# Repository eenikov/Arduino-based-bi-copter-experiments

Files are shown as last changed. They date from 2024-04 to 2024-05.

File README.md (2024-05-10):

# System Identification and Control Design Experiments with the Arduino-Based Bi-Copter Hardware 
## Eniko T Enkiov, University of Arizona
This project aims to demonstrate the use of MATLAB's system identification toolbox in developing dynamic models of an Arduino-Based aero-mechatronic system. The system is comprised of two propellers mounted on a pivoting arm, along with Arduino Nano 33 IoT and a battery pack. It is operated wirelessly via local WiFi network using MATLAB's Simulink Arduino support package. Except for the 3D printed arm and stand, all other components are commercially available, allowing easy replication of the experiment. Additionally, a Simscape model replicates the hardware-based experience for users who prefer virtual experimentation.
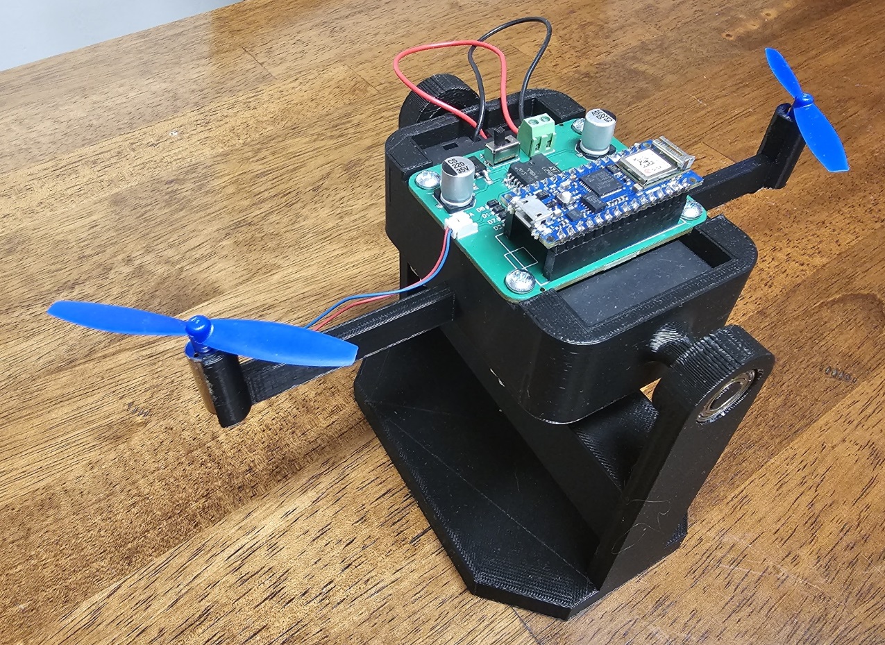
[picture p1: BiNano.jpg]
  

https://github.com/eenikov/BiCopter_SystemID_Project/assets/116908311/2a8902c1-a9a7-4af2-bafb-f2ca30b6aef8

## Learning Goals
- Obtain linear dynamic models from input-output data. Examples inlucde autoregressive models with exogenous input (ARX), state space model based on N4SID subspace method.
- Investigate the the effect of bandwidth and amplitude of the test input on the obtained model. 
- Evaluate different model orders using physical and numerical considerations (creiteria such as autocorrelelation and cross correlation of the resiudual)
- Learn how to design closed-loop controllers using PID and state space-based approaches. 

## Setup
- [Bi-copter 3D printing instructions](https://www.youtube.com/watch?v=3kPK0pJ30wg) (Download [SolidWorksFiles.zip](https://github.com/eenikov/BiCopter_SystemID_Project/blob/main/SolidWorksFiles.zip) and print  Stand, Arms, and 2x Bearing Caps using a 3D printer of your choice.)
-Download the controller circuit board files [PCB.zip](https://github.com/eenikov/BiCopter_SystemID_Project/blob/main/PCB.zip) and place an order with [https://jlcpcb.com/](https://jlcpcb.com/) to produce a PCB with the motor drivers. You will need to purchase the reaming parts from AMAZON.COM and assemble the pendulum per the instructions in the video below.
-  Download the bill of materials/parts [Bill_of_Materials.xlsx](https://github.com/eenikov/Arduino-based-bi-copter-experiments/blob/main/Bill_Of_Materials.xlsx) and purchase from AMAZON or other vendor of your choice.
- [Follow the Bi-Copter assembly instructions](https://www.youtube.com/watch?v=vzXoB-3JaGU)
- Download and install low-cost hardware support packages:
  * [Simulink Support Package for Arduino](https://www.mathworks.com/hardware-support/arduino.html#simulink)
  * [MATLAB Support Package for Arduino](https://www.mathworks.com/hardware-support/arduino.html#matlab)
 
## Experiments with the physical hardware (based on Livescript and three Simulink models operating the Bi-Copter
- Download [Bicopter_Hardware_Experiments](https://github.com/eenikov/Arduino-based-bi-copter-experiments/tree/main/Bicopter_Hardware_Experiments) repository and launch  [Run_Bicopter_Experiments.mlx](https://github.com/eenikov/Arduino-based-bi-copter-experiments/blob/main/Bicopter_Hardware_Experiments/Run_Bicopter_Experiments.mlx) live script. Follow instructions with the script. Run section by section.

## Experiments with a Simscape Model (alternative to the physical experiment)
- Download [Bicopter_Virtual_Experiments](https://github.com/eenikov/Arduino-based-bi-copter-experiments/tree/main/Bicopter_Virtual_Experiments) repository and launch [BiCopter_Simulation.mlx](https://github.com/eenikov/Arduino-based-bi-copter-experiments/blob/main/Bicopter_Virtual_Experiments/BiCopter_Simulation.mlx)  live script. Follow instructions with the Live Script. Run section by section.

## Additional Resources
- [System Identification Tech Talks](https://www.mathworks.com/videos/series/system-identification.html)
- [MATLAB Onramp](https://www.mathworks.com/learn/tutorials/matlab-onramp.html) – a free two-hour introductory tutorial that teaches the essentials of MATLAB.
- [Simulink Onramp](https://www.mathworks.com/learn/tutorials/simulink-onramp.html) – a free three-hour introductory tutorial that teaches the essentials of Simulink.
- [Control Design Onramp with Simulink](https://matlabacademy.mathworks.com/details/control-design-onramp-with-simulink/controls) - learn the basics of feedback control design in Simulink.

## Products
MATLAB, Simulink, System Identification Toolbox™, Control System Toolbox™, Simscape™, Simscape Multibody™

## Educator Resources
- [MATLAB and Simulink Courseware](https://www.mathworks.com/academia/courseware.html)
- [Teaching Controls with MATLAB and Simulink](https://www.mathworks.com/academia/courseware/teaching-controls-with-matlab-and-simulink.html)
- [Teaching Modeling and Controls using MATLAB Live Scripts](https://www.mathworks.com/videos/teaching-modeling-and-controls-with-the-matlab-live-editor-1623992486476.html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)

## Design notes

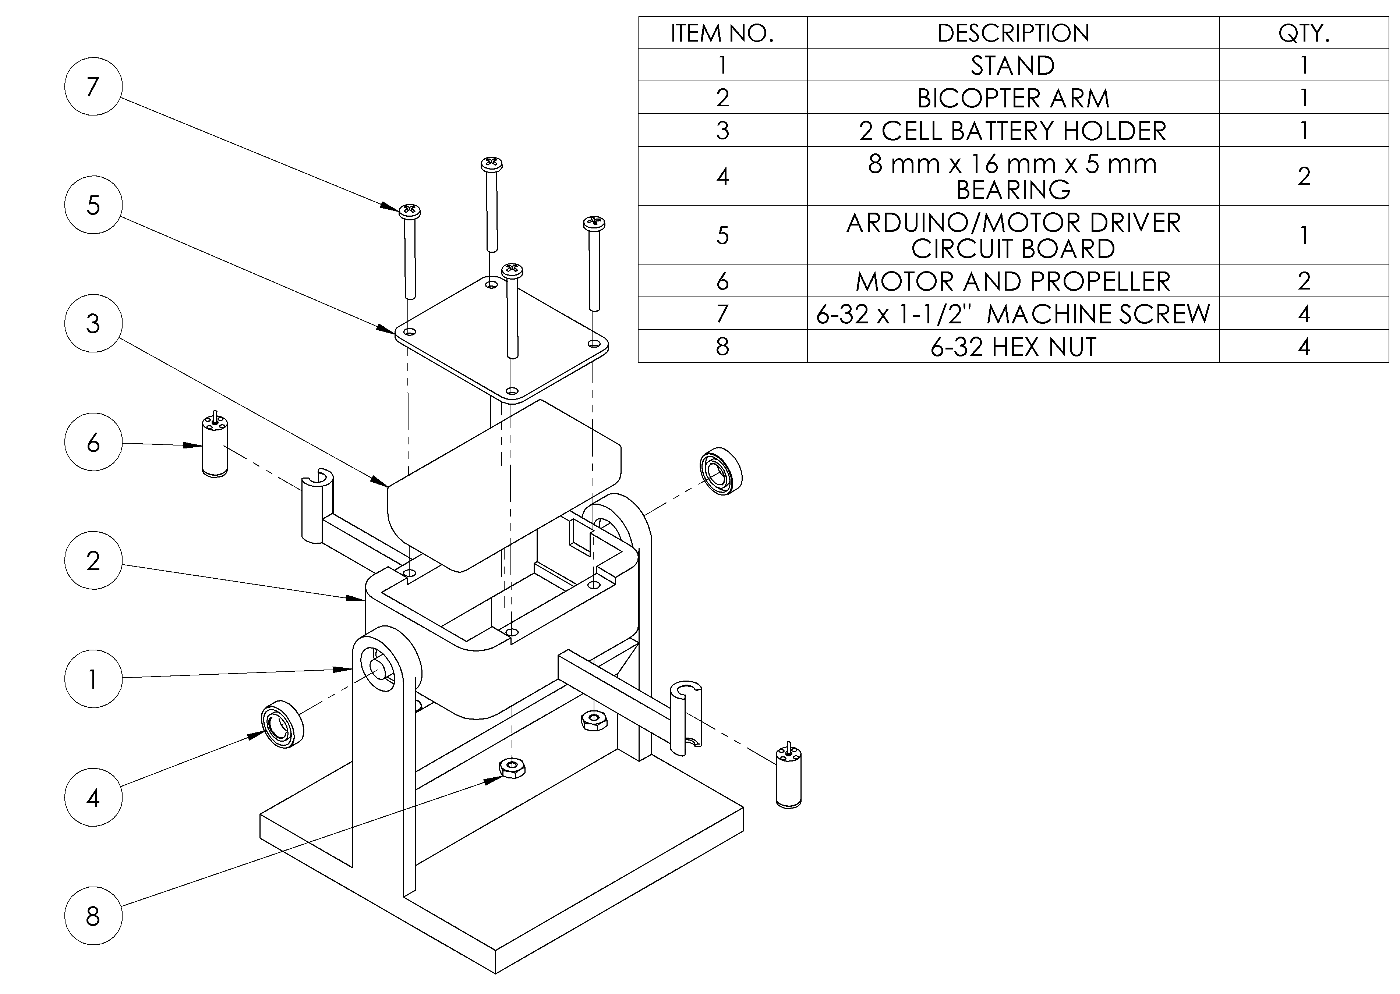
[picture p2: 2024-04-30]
SolidWorksFiles/Assem1.PNG

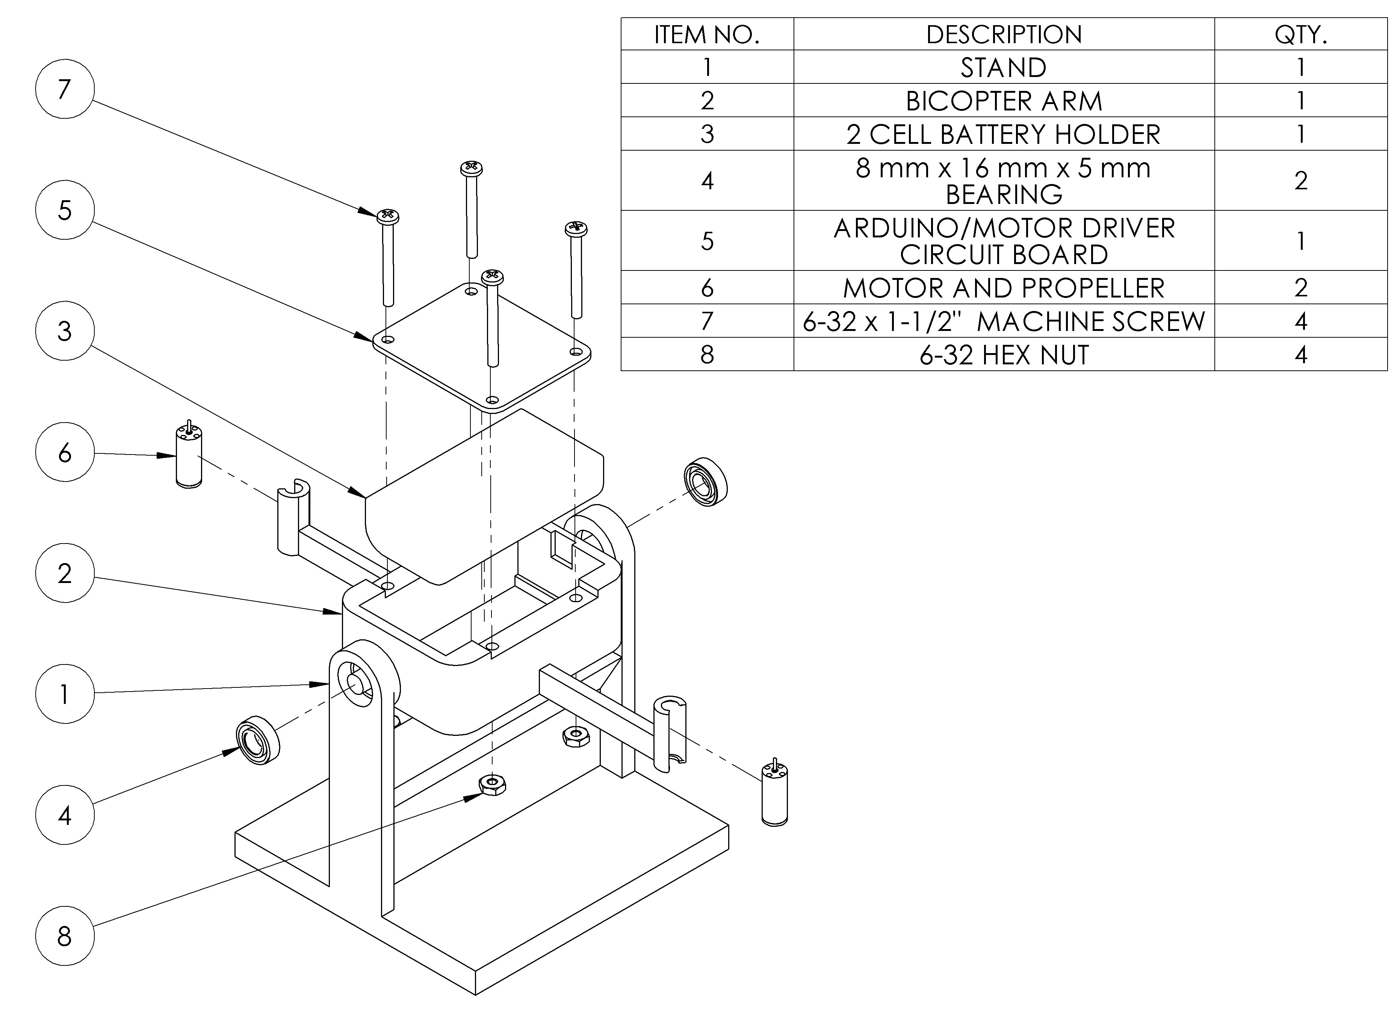
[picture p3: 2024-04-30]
SolidWorksFiles/Assem1.JPG

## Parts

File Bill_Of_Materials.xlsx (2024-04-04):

ITEM NO. | DESCRIPTION | QTY. | AMAZON LINK
1 | STAND | 1
2 | BICOPTER ARM | 1
4 | 8 mm x 16 mm x 5 mm BEARING | 2 | https://www.amazon.com/uxcell-Bearing-Shielded-2080088-Bearings/dp/B07FW2YKL8/
6 | MOTOR AND PROPELLER | 2 | https://www.amazon.com/Funny-Utopic-8-5x20mm-Connector-Quadcopter/dp/B07PLV3C2K https://www.amazon.com/dp/B019W2QDNO/
5 | 6-32 x 1-1/2" MACHINE SCREW (OR M4X35) | 4 | https://www.amazon.com/Prime-Line-9003284-Machine-Phillips-Stainless/dp/B074ZZ2K8Z/
6 | 6-32 HEX NUT (OR M4) | 4 | https://www.amazon.com/Prime-Line-9074040-Machine-Stainless-50-Pack/dp/B074ZMZZKS/
7 | ARDUINO/MOTOR DRIVER CIRCUIT BOARD | 1
8 | 2 CELL BATTERY HOLDER | 1 | https://www.amazon.com/Battery-Storage-Plastic-Batteries-YOUCHENG/dp/B08LZ3553W/ https://www.amazon.com/TOPUSSE-Rechargeable-Battery-2500mAh-Current/dp/B0C1NNXKW1/?th=1

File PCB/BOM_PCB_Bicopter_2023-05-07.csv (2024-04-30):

ID | Name | Designator | Footprint | Quantity | Manufacturer Part | Manufacturer | Supplier | Supplier Part | Price
1 | AS7805ADTR-G1 | U1 | TO-252-2_L6.6-W6.1-P4.57-LS9.9-BR-CW | 1 | AS7805ADTR-G1 | DIODES(美台) | LCSC | C294595 | 0.219
2 | POWER | SW1 | SW-TH_SS-12D02-VG4 | 1 | SS-12D02-VG4 | Rectangular Connectors - Contacts | LCSC | C136719 | 0.073
3 | 220uF | U4,U5 | CAP-SMD_BD8.0-L8.3-W8.3-FD | 2 | CS220UF35V167RV0148 | KNSCHA(科尼盛) | LCSC | C5250965 | 0.07
4 | L298P | U6 | POWERSO20_L15.9-W11.0-P1.27-LS14.2-BL-EP | 1 | L298P | ST(意法半导体) | LCSC | C85595 | 12.272
5 | Vin | U9 | CONN-TH_2P-P3.50_JL124D-35002G01 | 1 | JL124D-35002G01 | JILN | LCSC | C415432 | 0.142
6 | MOTOR A | CN1 | CONN-TH_530480210 | 1 | 530480210 | MOLEX | LCSC | C505099 | 0.155
7 | MOTOR B | CN2 | CONN-TH_530480210 | 1 | 530480210 | MOLEX | LCSC | C505099 | 0.155
8 | HDR-F-2.54_1x15 | H1,H2 | HDR-F-2.54_1X15 | 2 |  |  | LCSC | C124408 | 0.204
9 | 1N4007-C181127 | D1,D2,D3,D4,D5,D6,D7,D8 | SOD-123F_L2.8-W1.8-LS3.7-RD | 8 | 1N4007L | Hottech(合科泰) | LCSC | C181127 | 0.007

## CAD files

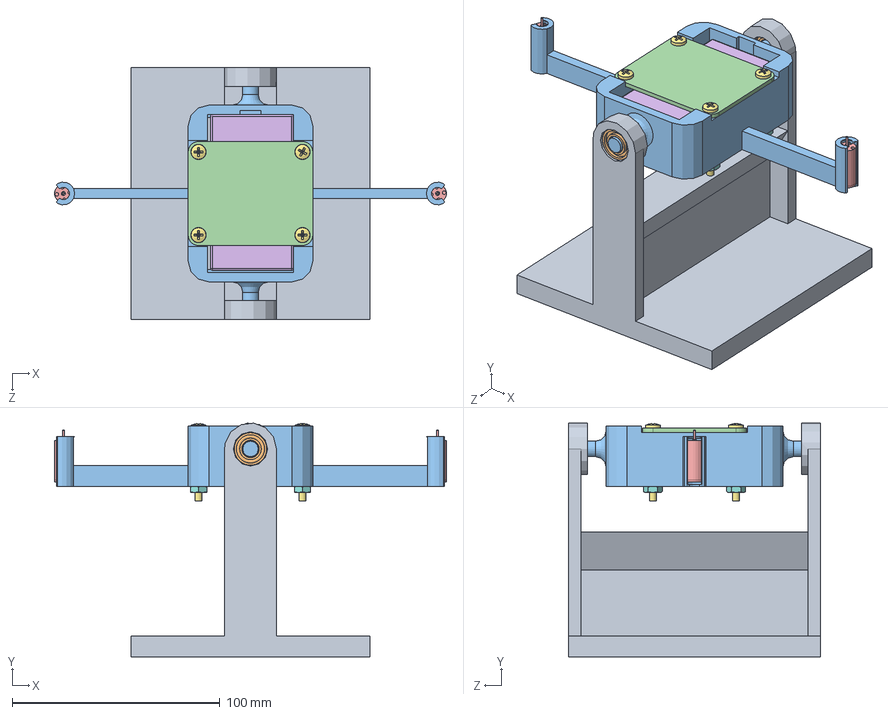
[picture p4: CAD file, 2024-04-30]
SolidWorksFiles/Assem1.SLDASM
188.5 x 112.4 x 121.0 mm
stand
radial ball bearing_68_am x 2
arms
board
8520 Coreless Brshed motor.step x 2
battery_holder
binding head screw_ai x 4
machine screw nut hex_ai x 4

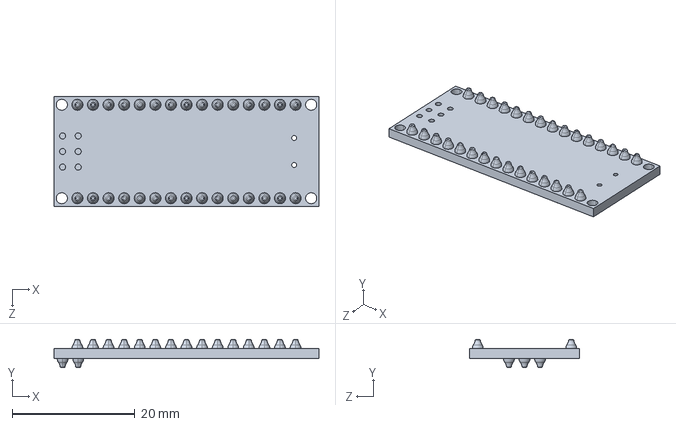
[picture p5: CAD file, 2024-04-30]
Bicopter_Virtual_Experiments/nano-board_Default_sldprt.STEP
43.2 x 4.60 x 18.0 mm

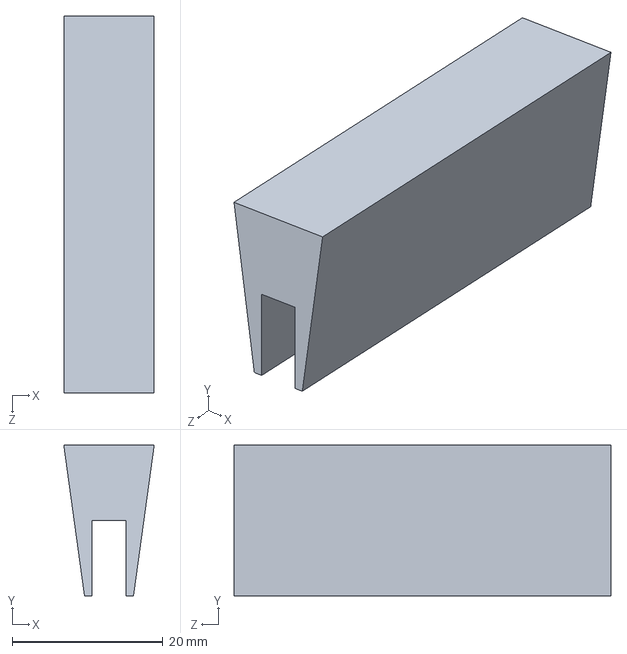
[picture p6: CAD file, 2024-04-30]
SolidWorksFiles/spacer.SLDPRT
12.0 x 20.0 x 50.0 mm

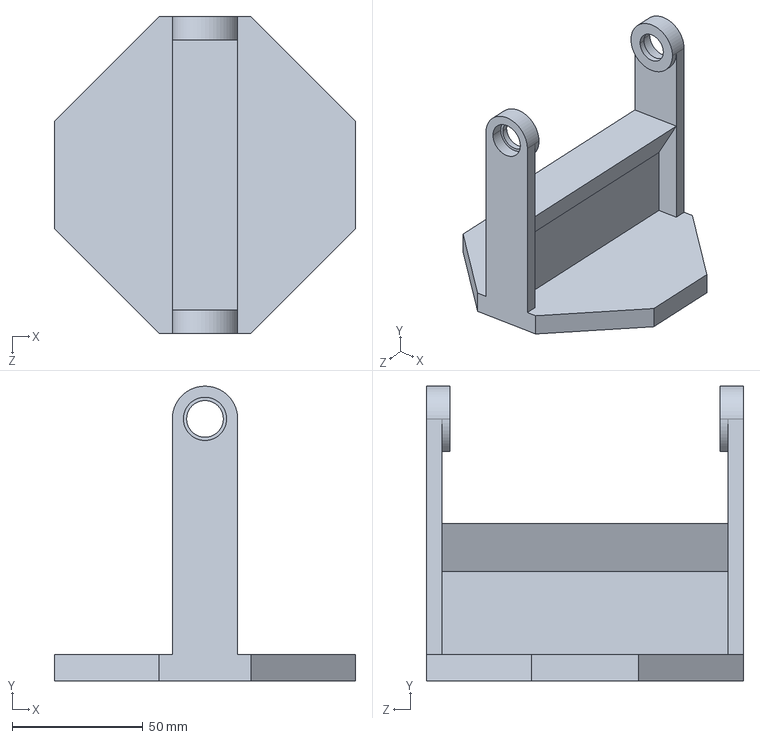
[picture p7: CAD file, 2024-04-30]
Bicopter_Virtual_Experiments/stand_Default_sldprt.STEP
115.0 x 112.5 x 121.0 mm

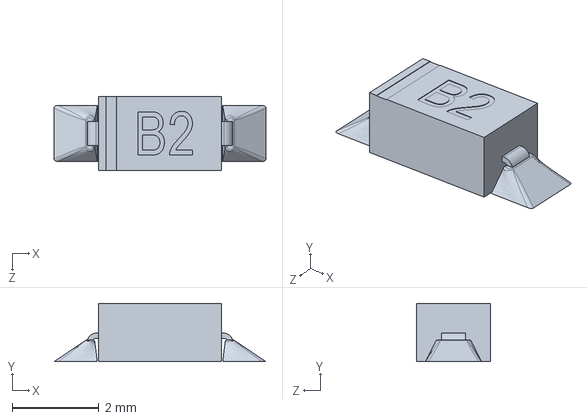
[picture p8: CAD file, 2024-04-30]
Bicopter_Virtual_Experiments/NANO DIODE_Default_sldprt.STEP
4.90 x 1.35 x 1.70 mm

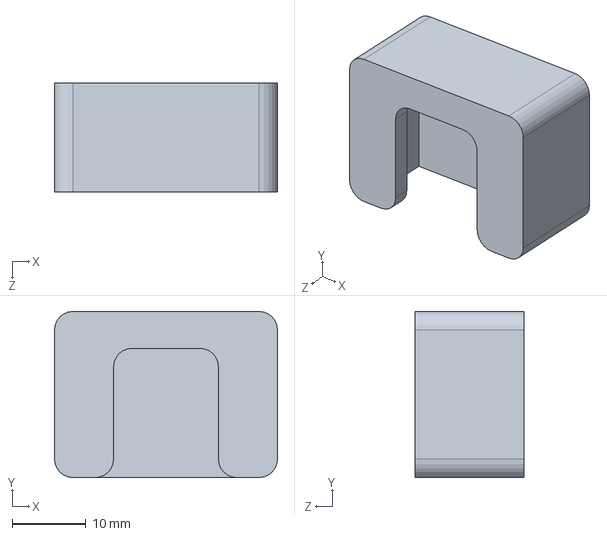
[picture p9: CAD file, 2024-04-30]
SolidWorksFiles/Ball Bearing Cap.SLDPRT
30.2 x 22.5 x 14.8 mm

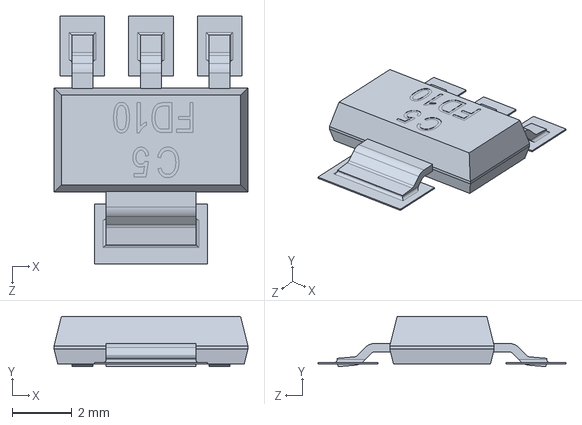
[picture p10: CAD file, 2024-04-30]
Bicopter_Virtual_Experiments/nano - reg_Default_sldprt.STEP
6.50 x 1.69 x 8.30 mm

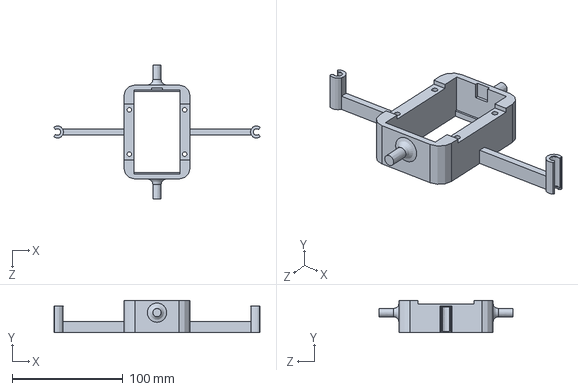
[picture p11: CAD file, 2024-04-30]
SolidWorksFiles/arms.SLDPRT
186.4 x 29.0 x 121.0 mm

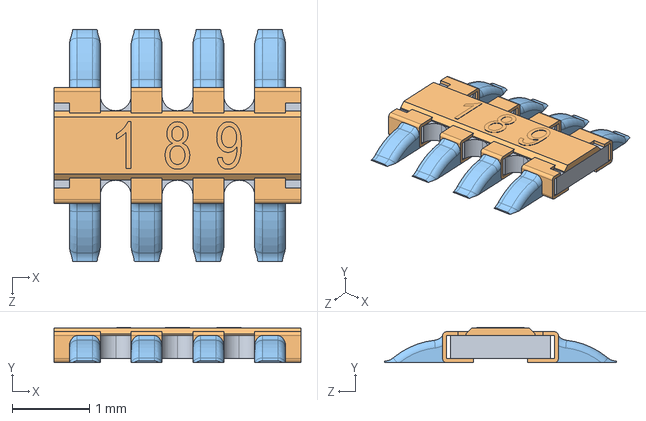
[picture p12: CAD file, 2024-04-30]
Bicopter_Virtual_Experiments/189 RESISTOR PACK_Default_sldprt.STEP
3.20 x 0.455 x 3.00 mm

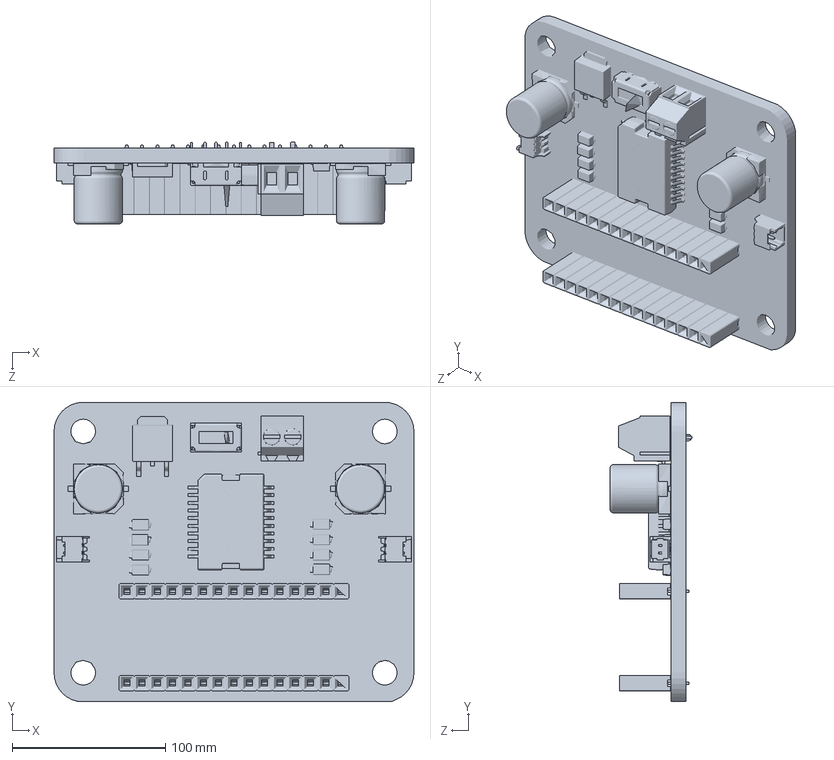
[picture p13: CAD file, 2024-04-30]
SolidWorksFiles/OBJ_PCB_Bicopter.SLDPRT
235.0 x 195.5 x 53.3 mm

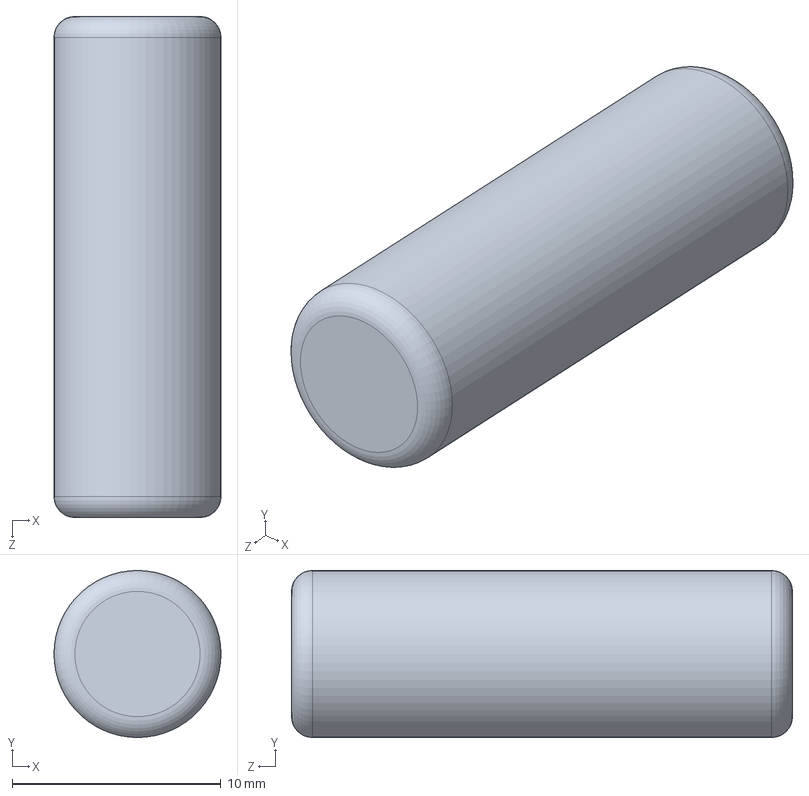
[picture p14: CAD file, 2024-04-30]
Bicopter_Virtual_Experiments/motor.SLDPRT
8.00 x 8.00 x 24.0 mm

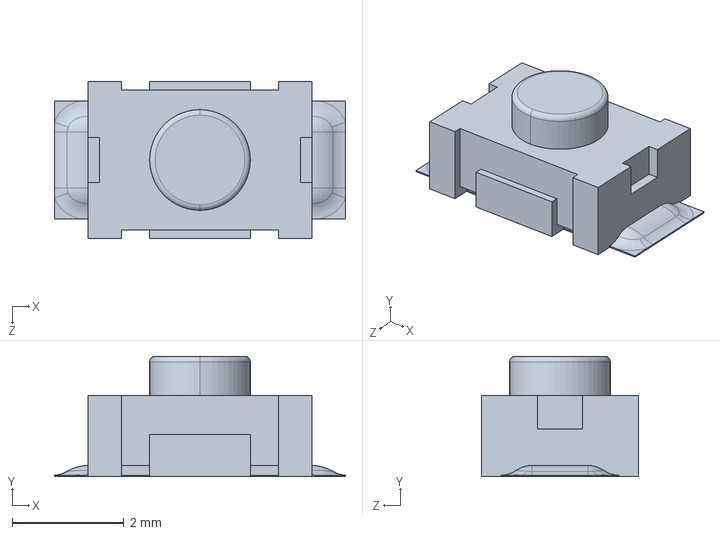
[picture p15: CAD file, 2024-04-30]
Bicopter_Virtual_Experiments/reset core_Default_sldprt.STEP
5.20 x 2.15 x 2.80 mm

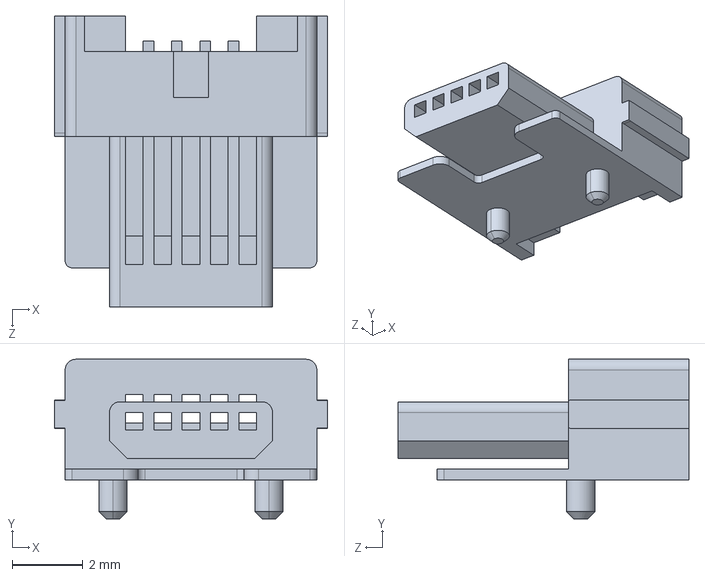
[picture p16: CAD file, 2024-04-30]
Bicopter_Virtual_Experiments/MINIUSBCORE_Default_sldprt.STEP
7.70 x 4.50 x 8.20 mm

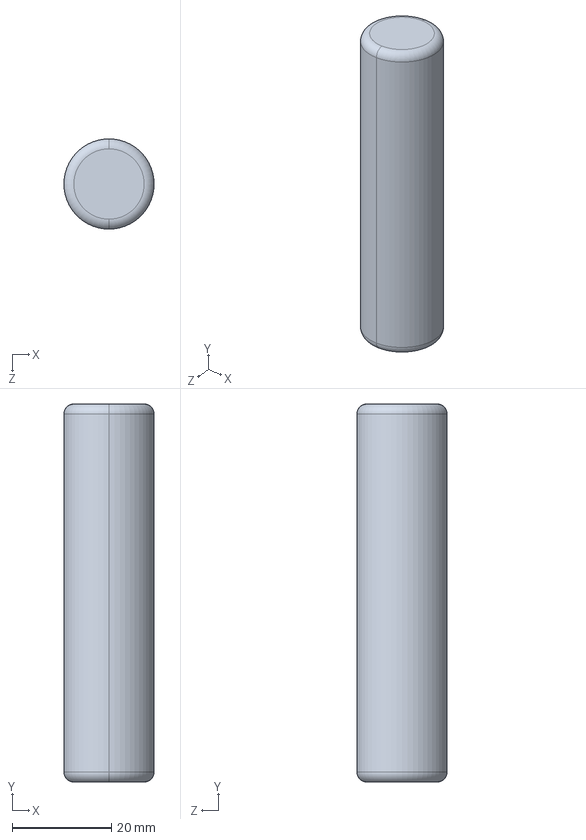
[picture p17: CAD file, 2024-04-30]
Bicopter_Virtual_Experiments/battery_Default_sldprt.STEP
18.1 x 76.0 x 18.1 mm

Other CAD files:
Bicopter_Virtual_Experiments/arduino nano.SLDASM
SolidWorksFiles/stand.SLDPRT
Bicopter_Virtual_Experiments/arms_Default_sldprt.STEP
Bicopter_Virtual_Experiments/reset shell_Default_sldprt.STEP
Bicopter_Virtual_Experiments/102 RESISTOR PACK_Default_sldprt.STEP
Bicopter_Virtual_Experiments/16mhz crystal - measured_Default_sldprt.STEP
Bicopter_Virtual_Experiments/MINI USB CONTACT_Default_sldprt.STEP
Bicopter_Virtual_Experiments/MINIUSBSHELL_Default_sldprt.STEP
Bicopter_Virtual_Experiments/PCB_Default_sldprt.STEP
Bicopter_Virtual_Experiments/PropellerRED_Default_sldprt - Copy.STL
Bicopter_Virtual_Experiments/PropellerRED_Default_sldprt.STEP
Bicopter_Virtual_Experiments/PropellerRED_Default_sldprt.STL
Bicopter_Virtual_Experiments/arms_Default_sldprt.STL
Bicopter_Virtual_Experiments/cap106C_Default_sldprt.STEP
Bicopter_Virtual_Experiments/ftdi FT232rl_Default_sldprt.STEP
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

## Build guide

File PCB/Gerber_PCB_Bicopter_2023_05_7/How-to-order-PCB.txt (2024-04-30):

How to Order PCB

Please refer to:
https://docs.easyeda.com/en/PCB/Order-PCB

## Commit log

2024-05-10 some message
    [102 RESISTOR PACK_Default_sldprt.STEP, 16mhz crystal - measured_Default_sldprt.STEP, 189 RESISTOR PACK_Default_sldprt.STEP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]
2024-05-10 renamed bom
    [Bill_Of_Materials.xlsx]
